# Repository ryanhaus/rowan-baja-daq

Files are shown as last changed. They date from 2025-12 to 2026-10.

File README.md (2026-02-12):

# Rowan University Baja DAQ System
This repository contains all files related to the Data Acqusition (DAQ) system for Rowan University's Baja SAE 2025-2027 team.

All files in this repository are licensed under the [GNU General Public License Version 3.0](LICENSE).

## Components
Click these links to quickly navigate to one of the several components of the DAQ system.
Each link has more detailed information about the design and use of the component.
 - [CAN Module](can-module): Main building block of design, connects other devices together over the CAN bus.

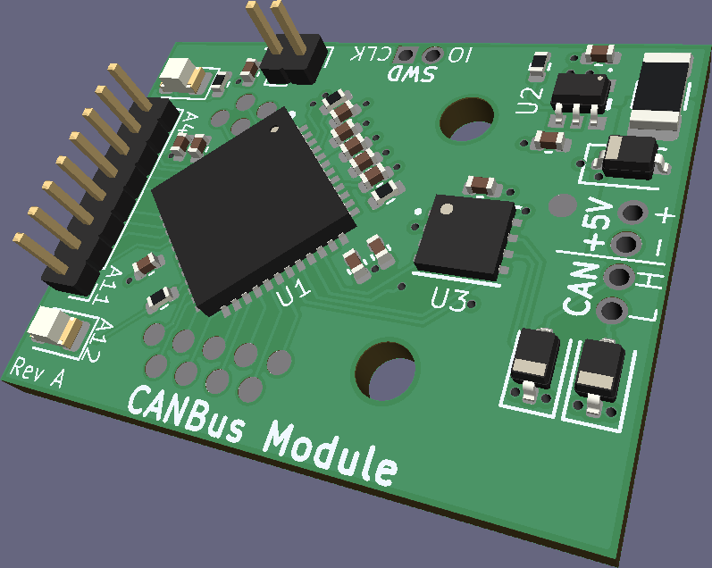
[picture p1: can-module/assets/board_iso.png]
   

 - [Accelerometer Board](accelerometer-board): Contains a 6-axis intertial measurement unit to measure linear and rotational acceleration.

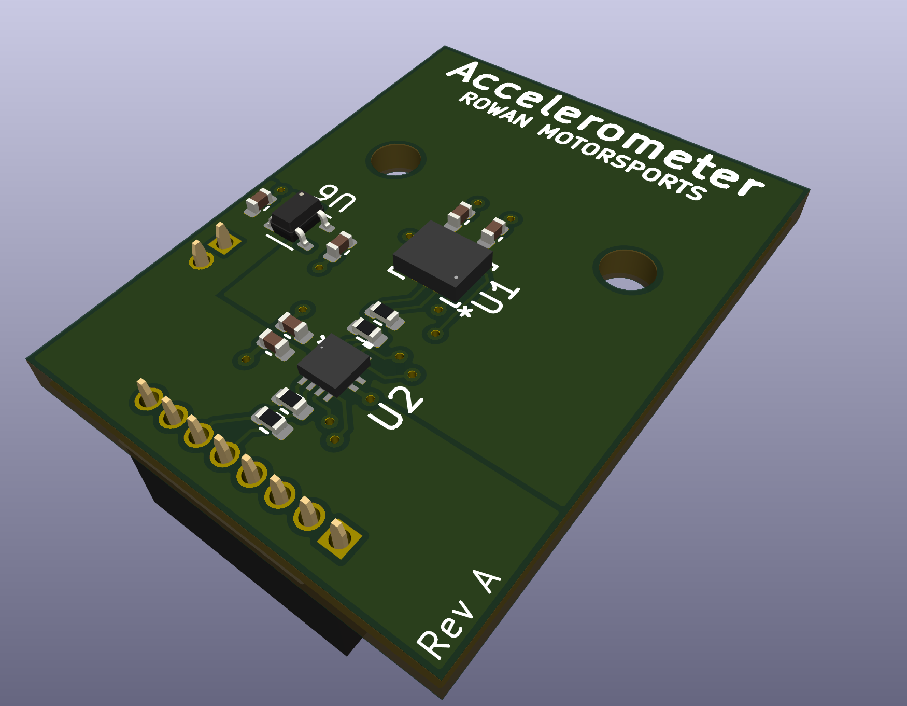
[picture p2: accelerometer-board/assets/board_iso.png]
   

 - [SD Card Board](sd-card-board): Contains a microSD card slot to log data.

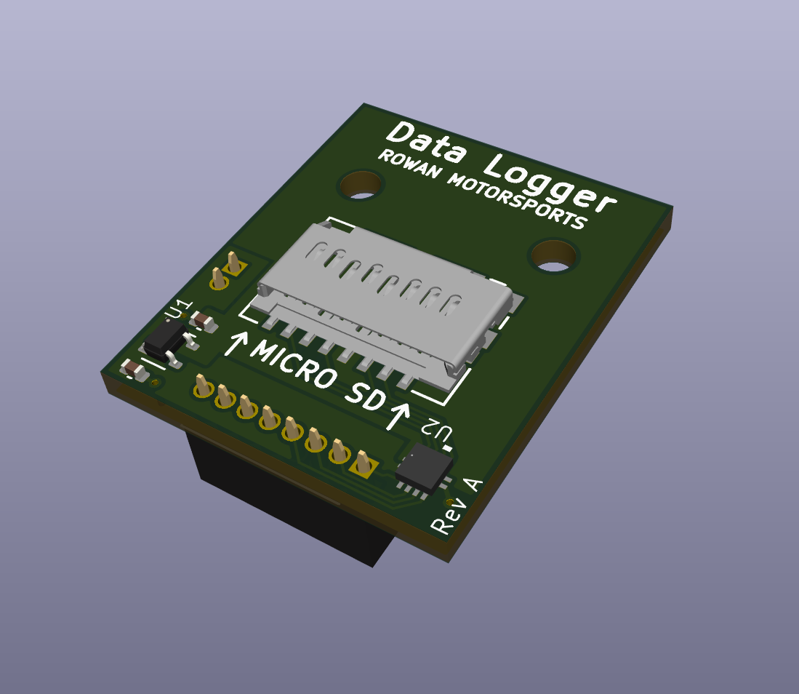
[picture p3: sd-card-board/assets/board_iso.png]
   

 - [Wireless Communication Unit](comm-unit): Contains a LoRa module to wirelessly transmit data.

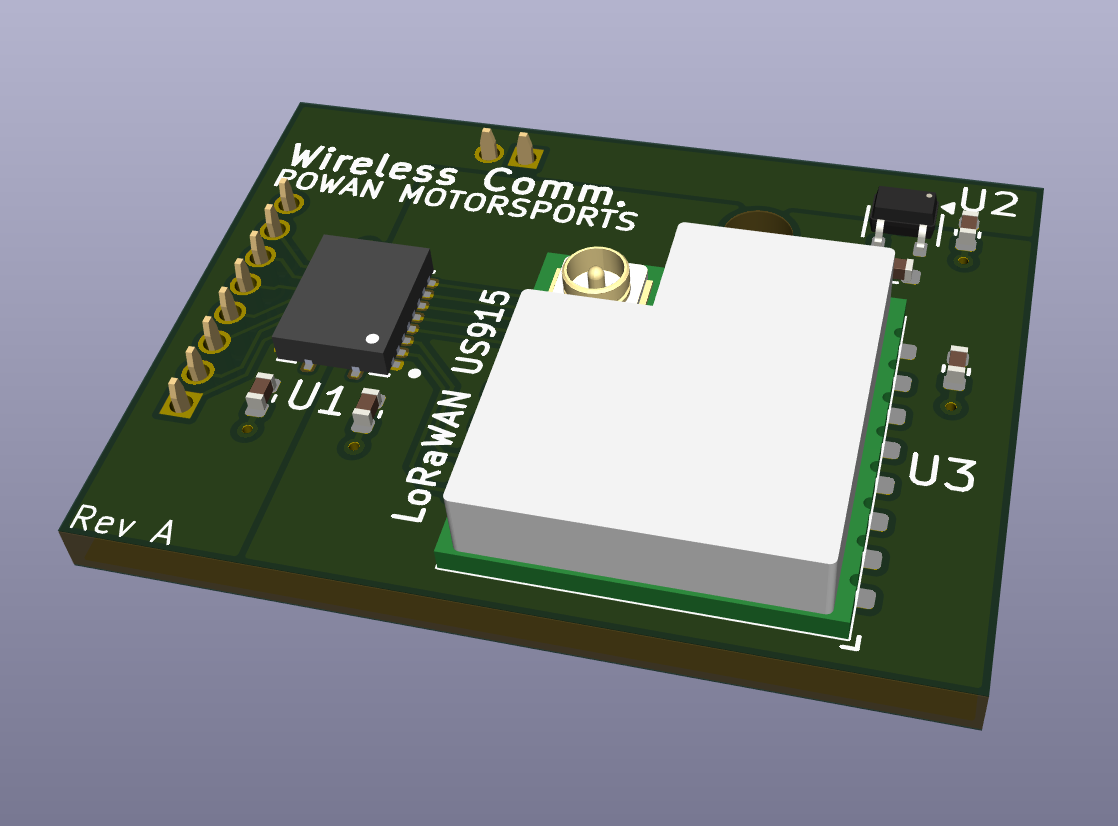
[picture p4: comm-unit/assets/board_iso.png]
   

 - [PMOD Adapter](pmod-adapter): Allows PMOD boards to be attached to the CAN Modules.

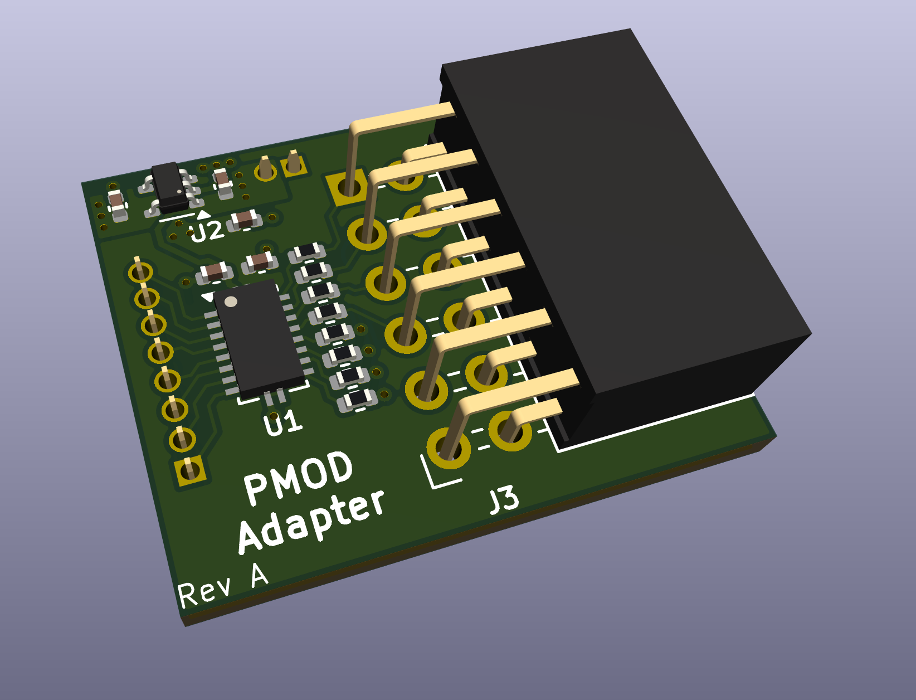
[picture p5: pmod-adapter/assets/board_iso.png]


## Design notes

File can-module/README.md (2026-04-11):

# CAN Module
The CAN Module is the main building block for the overall Data Acquisition system.
It is used as an interface between the shared [CAN Bus](https://en.wikipedia.org/wiki/CAN_bus) and each individual sensor or module around the vehicle.
This document holds all documentation about the components and usage for the CAN Module PCB.

Screenshot of board

See the [software](software) and [pcb](pcb) directories for more info on the respective topics.

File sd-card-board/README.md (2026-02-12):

# SD Card Board
This board is a small data logger board that is designed to mount as a daughterboard for the [CAN Module](../can-module).
A microSD card can be inserted into it and the CAN Module will be able to communicate with the card.
The board features a 5V <=> 3.3V logic level converter to allow communication between the CAN Module and the microSD card.

Board

> [!NOTE]
> The SD card will be operating in SPI mode, so data bandwidth will be somewhat limited.

## Schematic
A screenshot of the schematic is below, a higher-quality pdf is available [here](assets/schematic.pdf).

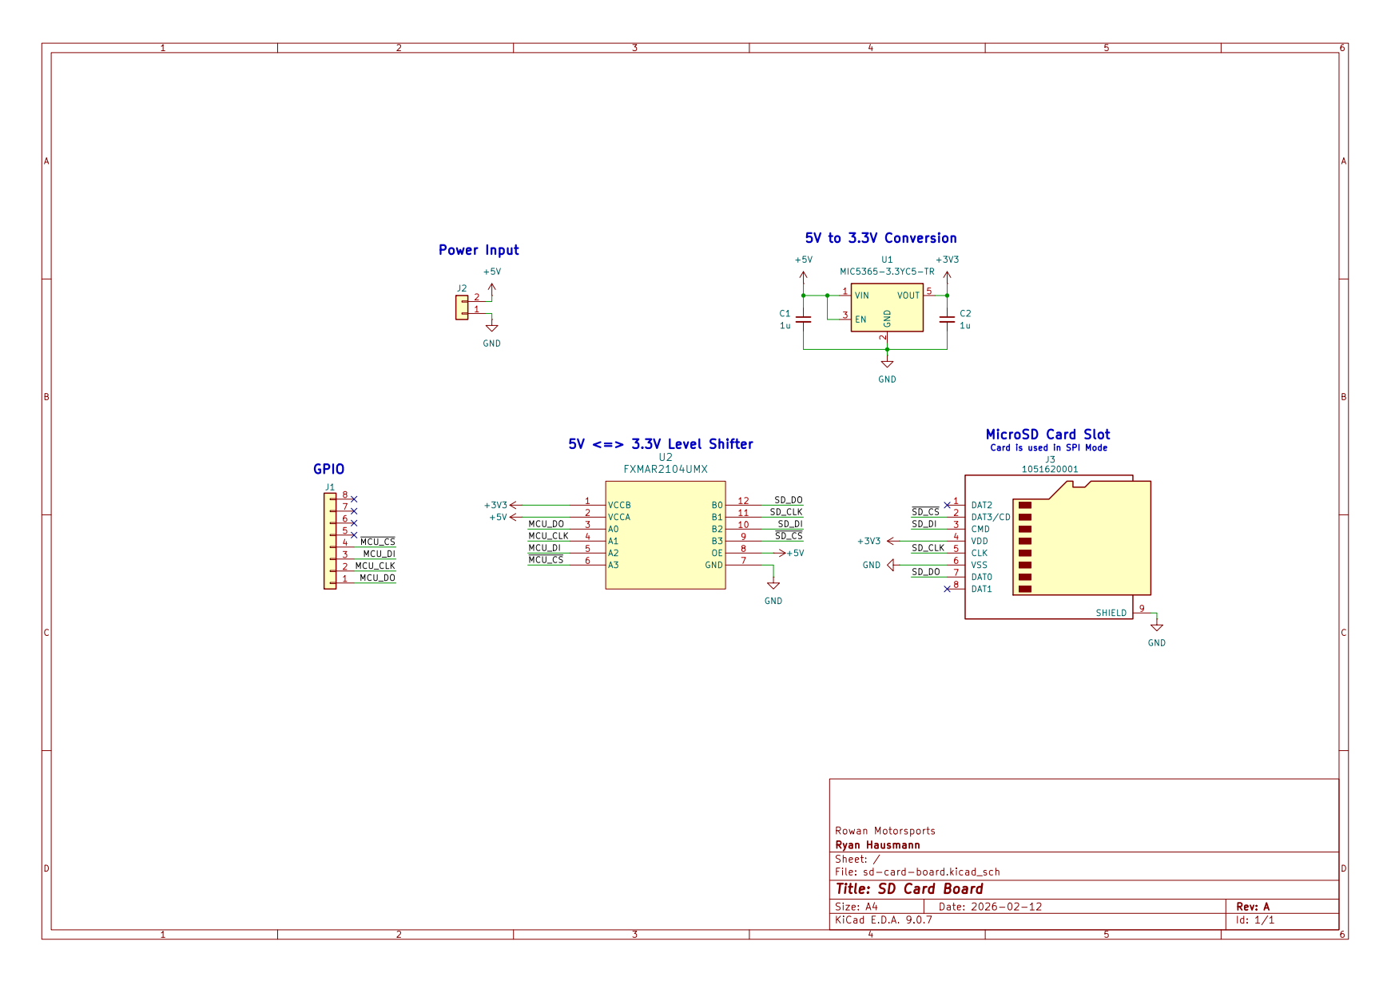
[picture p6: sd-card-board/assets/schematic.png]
Schematic


## Pins
| CAN Module | SD Card Board |
| --- | --- |
| A4 | N/C |
| A5 | N/C |
| A6 | N/C |
| A7 | N/C |
| A8 | CSn |
| A9 | DI |
| A10 | CLK |
| A11 | DO |

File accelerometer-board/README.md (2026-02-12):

# Accelerometer Board
This board features an BMI323 inertial measurement unit w/ a 6-axis accelerometer.
It is meant to be a daughterboard for the [CAN Module](../can-module) and is able to mount to the sensor interface and be attached with 2x M2 mounting screws.
The board also features a 5V <=> 3.3V logic level converter to allow for communication between the CAN Module and the IMU.

Image of board

## Schematic
Screenshot of schematic is below. Higher-quality pdf available [here](assets/schematic.pdf)

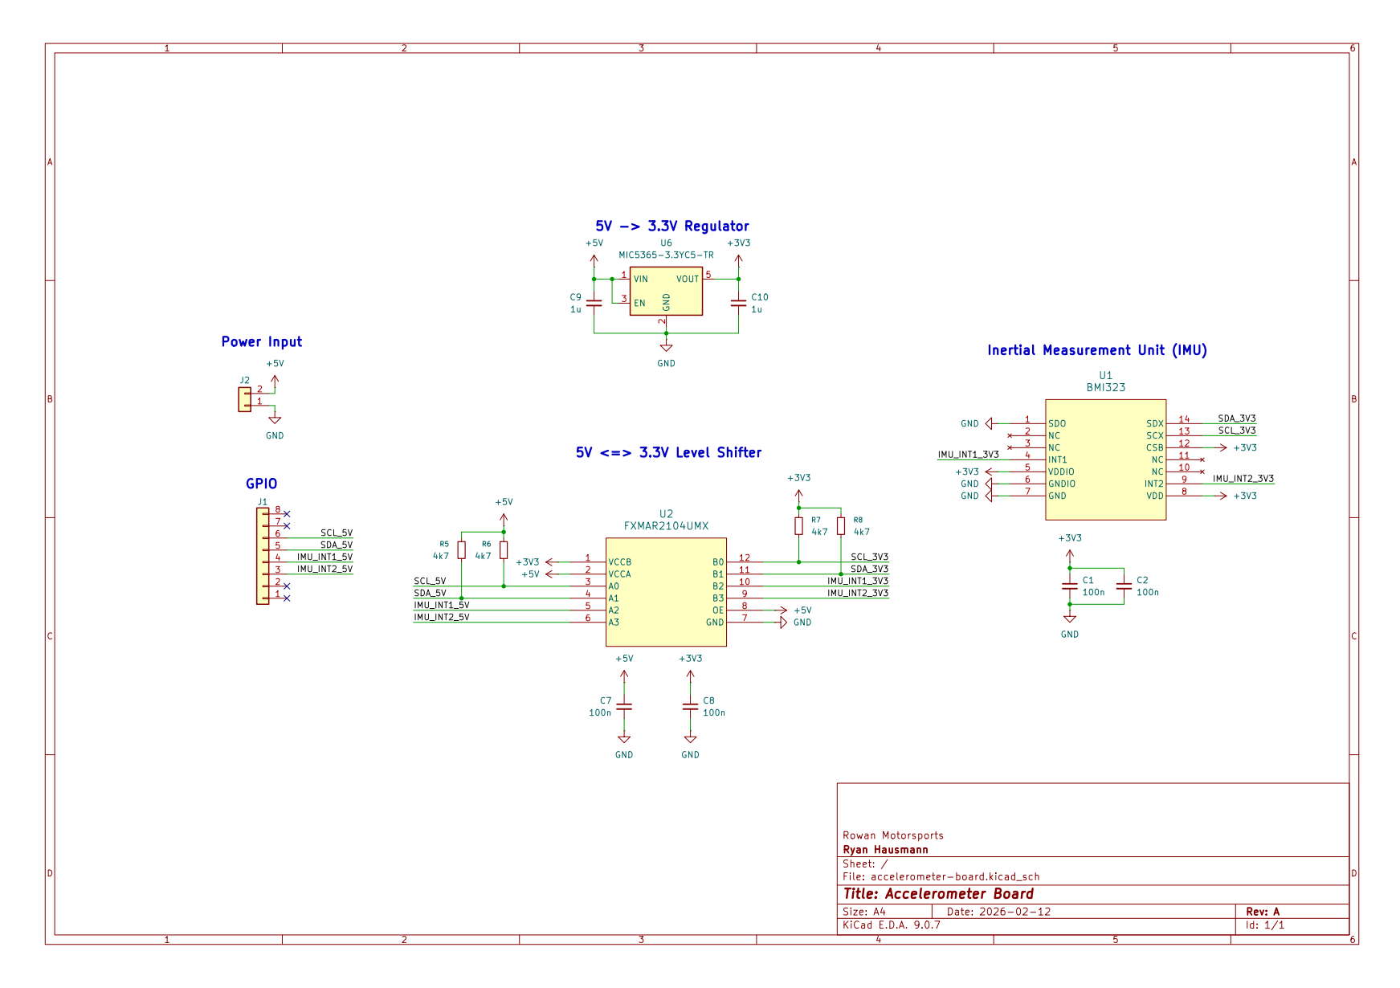
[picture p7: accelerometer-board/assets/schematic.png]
Schematic


## Pins
| CAN Module | Accelerometer Board |
| --- | --- |
| A4 | N/C |
| A5 | N/C |
| A6 | SCL |
| A7 | SDA |
| A8 | Interrupt 1 |
| A9 | Interrupt 2 |
| A10 | N/C |
| A11 | N/C |

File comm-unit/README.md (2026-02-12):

# Wireless Communication Unit
This board features a [Wio-SX1262](https://www.seeedstudio.com/Wio-SX1262-Wireless-Module-p-5981.html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) LoRa module and is used to wirelessly transmit sensor data over long distances (3-5km).
It is designed to be a daughterboard for the [CAN Module](../can-module) and mounts on top of it via the sensor interface.

Board

## Schematic
A screenshot of the schematic is below. A higher-quality pdf is available [here](assets/schematic.pdf).

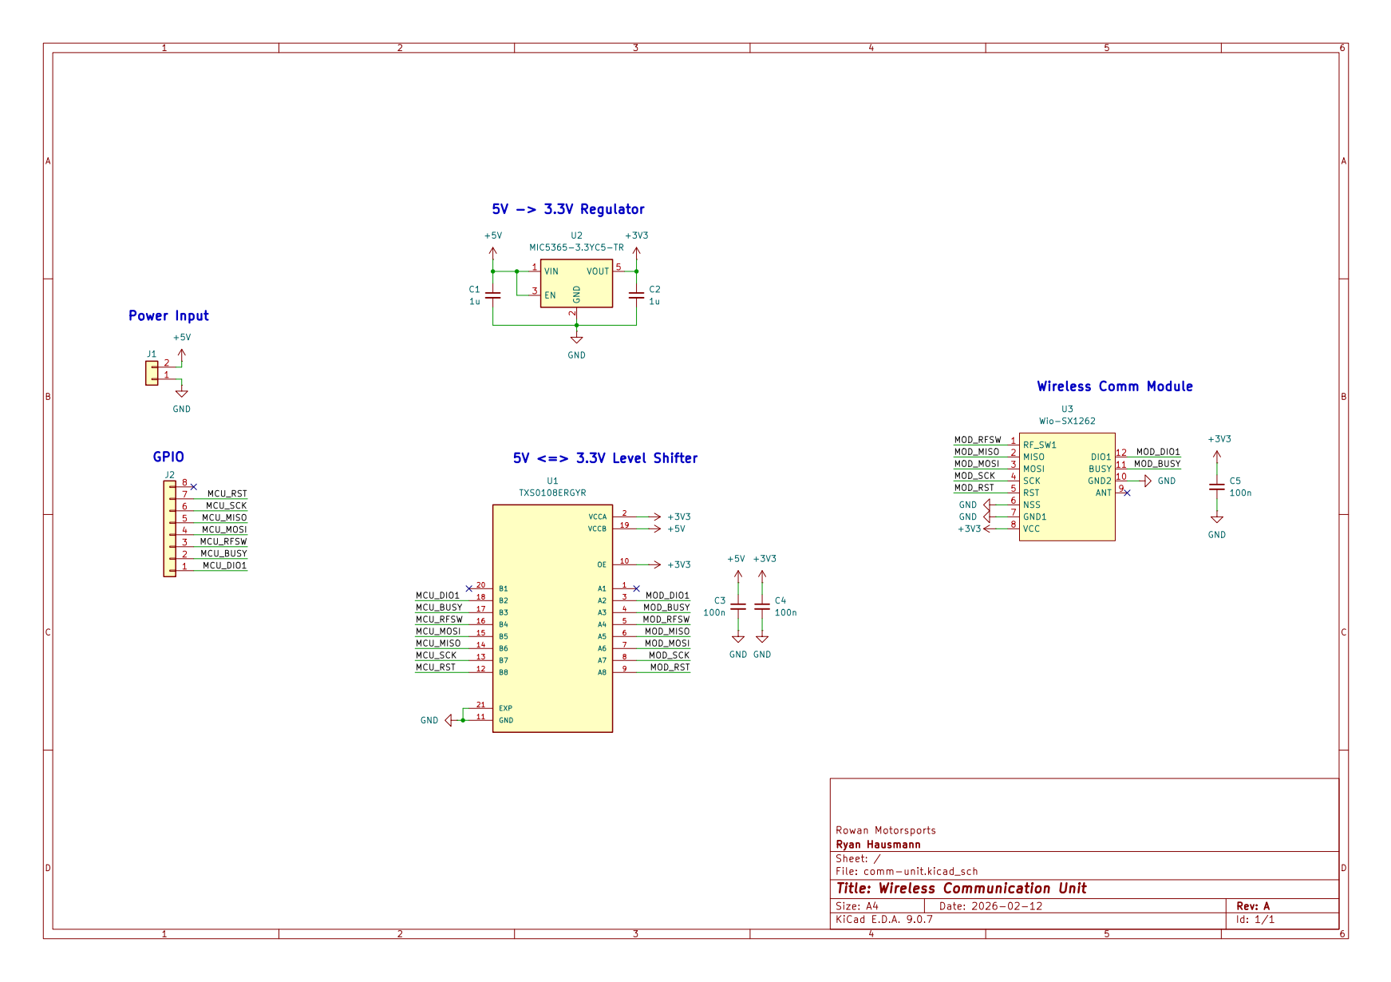
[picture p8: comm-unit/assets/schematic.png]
Schematic


## Pins
| CAN Module | Comm Unit |
| --- | --- |
| A4 | N/C |
| A5 | NRST |
| A6 | SCK |
| A7 | MISO |
| A8 | MOSI |
| A9 | RFSW |
| A10 | BUSY |
| A11 | DIO1 |

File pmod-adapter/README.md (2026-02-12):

# PMOD Adapter
The PMOD adapter is meant to be a daughterboard for the [CAN Module](../can-module).
It is meant to act as an adapter board to convert the 5V logic from the CAN Module into 3.3V logic for the [PMOD interface](https://en.wikipedia.org/wiki/Pmod_Interface) (see the spec [here](https://digilent.com/reference/_media/reference/pmod/pmod-interface-specification-1_2_0.pdf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)), which is commonly used in many [Digilent sensor boards](https://digilent.com/shop/products/fpga-boards/expansion-modules/pmods).
This helps save time when a single sensor needs to be used and it would be impractical to design a custom board just for that, making it easier to simply plug in a PMOD board.

Image of board

## Schematic
Screenshot of schematic is below. Higher quality pdf available [here](assets/schematic.pdf).

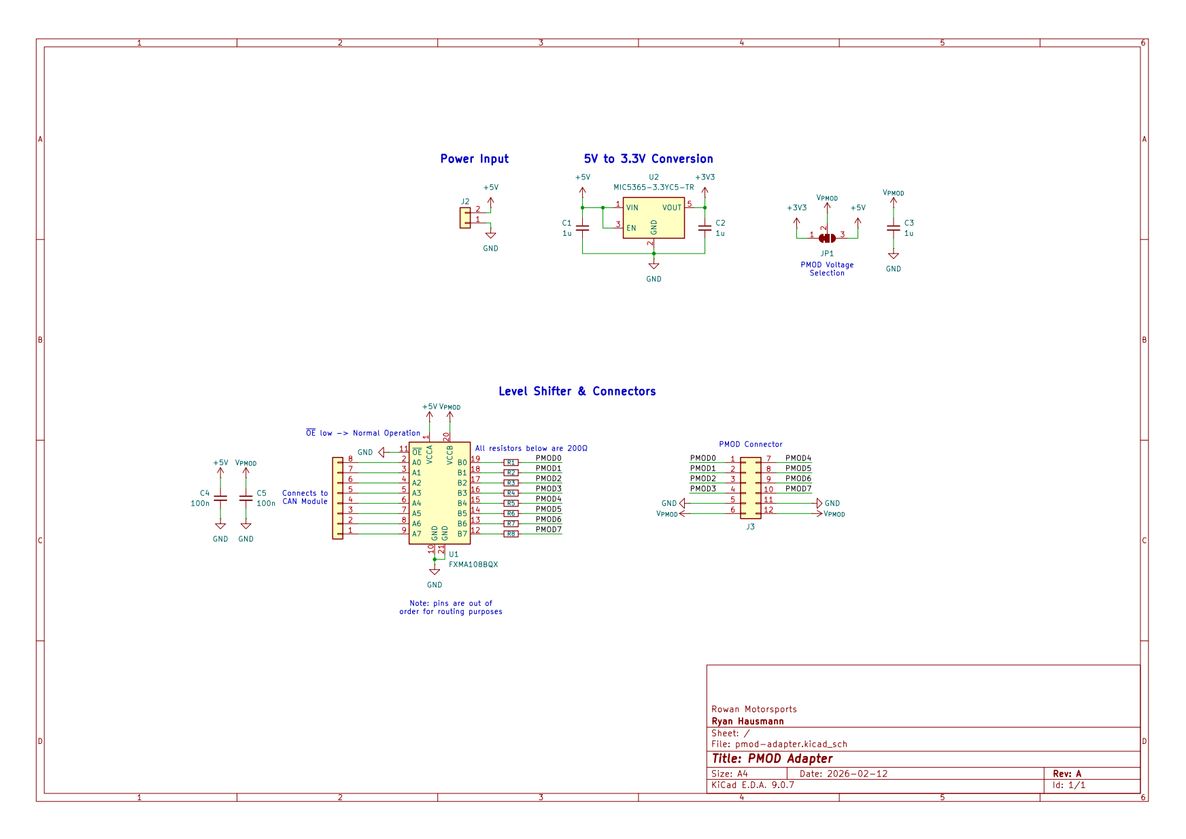
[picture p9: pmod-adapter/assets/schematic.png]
Schematic


## Pins
| CAN Module | PMOD Adapter |
| --- | --- |
| A4 | PMOD 0 |
| A5 | PMOD 1 |
| A6 | PMOD 2 |
| A7 | PMOD 3 |
| A8 | PMOD 4 |
| A9 | PMOD 5 |
| A10 | PMOD 6 |
| A11 | PMOD 7 |

## Extra Information
### Mounting to CAN Module
This board can mount directly onto the sensor interface of the CAN Module via female headers on the bottom of the board.
Note that, due to size constraints, this board does not feature M2 mounting holes.

### Changing the Logic Level
This board supports changing the logic level via a selectable solder bridge on the bottom of the board.
See the top right in the screenshot below:

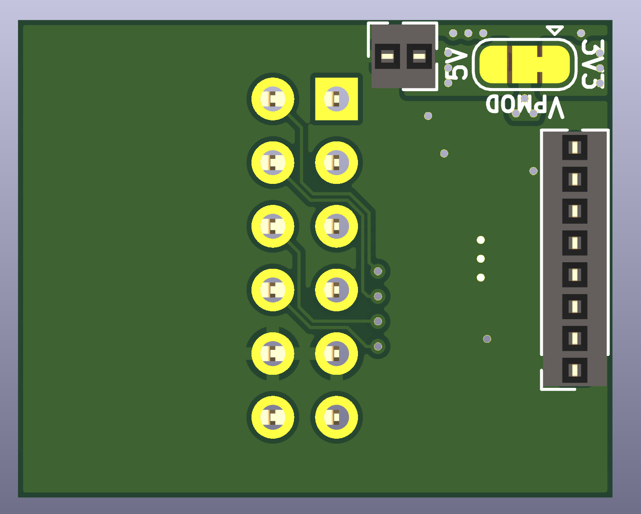
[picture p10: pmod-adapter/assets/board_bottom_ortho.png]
Image of bottom of board


> [!CAUTION]
> Note: When switching the logic level to 5V or something else, note that **the 3.3V bridge will have to be disconnected!!** Otherwise, this bridge will dead-short 5V to 3.3V.

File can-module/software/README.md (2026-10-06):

# Software
The software is written in the C programming language, and uses CMake as the build tool.

> [!NOTE]
> This has only been tested on Linux, unknown if it will work on Windows/Mac.
> If it doesn't work on Windows, you could try using [WSL](https://learn.microsoft.com/en-us/windows/wsl/install).

## Prerequisites
You will need the following:
 - [CMake](https://cmake.org/download/)
 - [MPLAB X IDE](https://www.microchip.com/en-us/tools-resources/develop/mplab-x-ide) (for PIC32 target)
    - You will need to install the packages for '32-bit MCUs' and 'XC32 Compiler' when prompted.
    - When installing the XC32 compiler, check the 'Add to PATH' option when prompted.
 - [ARM GCC Cross Compiler](https://developer.arm.com/downloads/-/gnu-rm) (for RP2040 target)
 - [pkg-config](https://gitlab.freedesktop.org/pkg-config/pkg-config) (for tests only)

### Quickstart on Linux
The following command can be used to install the required packages on Ubuntu or Fedora.
**Note that the XC32 compiler and MPLAB X IDE must be downloaded and installed separately from the vendor, see links above.**

#### Ubuntu
```sh
$ sudo apt install cmake libcriterion-dev pkg-config gcc-arm-none-eabi libnewlib-arm-none-eabi
```

#### Fedora
```sh
$ sudo dnf install cmake pkgconf-pkg-config arm-none-eabi-gcc-cs arm-none-eabi-newlib arm-none-eabi-gcc-cs-c++
$ rpm -ivh https://github.com/samber/criterion-rpm-package/releases/download/2.3.3/libcriterion-devel-2.3.3-2.el7.x86_64.rpm
```
Note that there is no provided package for libcriterion by default on Fedora, so [this](https://github.com/samber/criterion-rpm-package) package is manually installed separately above.
Additionally, libcriterion is only needed for tests.

## Building
To build, run the following:

```sh
$ cmake -B build # Generates CMake files, generally only needed once (unless you edit or add new CMake configs)
$ cmake --build build -j $(nproc) # Actually builds the targets
```

This will create build files and compile the target programs in the `build` directory.

## Running Tests
This project uses the Criterion testing library, which can be ran using CTest (included with CMake).

Tests need to be built within the `tests` directory. To build the tests, run the following within the `tests` directory (same commands for regular building, just run within the `tests` directory):
```sh
$ cmake -B build
$ cmake --build build -j $(nproc)
```

To run tests, run the following:

```sh
$ ctest --test-dir build
```

## Flashing to hardware
### Debugger
I used the [MPLAB SNAP](https://www.microchip.com/en-us/development-tool/pg164100) programmer/debugger connected to the SWD pins on the CAN module.

See Table 3.3.1 in the [user manual](https://ww1.microchip.com/downloads/aemDocuments/documents/DEV/ProductDocuments/UserGuides/MPLAB-Snap-In-Circuit-Debugger-User-Guide-50002787.pdf) to see the pinout needed for SWD. 

Note that the MPLAB SNAP will **not** provide power to the CAN Module, and it needs a voltage reference (5V) connected to the VDD pin. I made a simple wire harness to connect a +5V source to the VDD pin on the MPLAB SNAP and the +5V pin on the CAN Module, as well as connect all grounds. I also added wires to connect the SWDIO and SWCLK pins together between the MPLAB SNAP and CAN Module.

### How to flash PIC32
I used the MPLAB IPE software to flash the generated hex file in the `build/pic32` directory to the microcontroller.

Simply select the device as a `PIC32CM1216JH01048`, select the hex file for the target (located in `build/pic32` as `[name]_pic32.hex`), then click 'Program'.

### How to flash Raspberry Pi Pico (RP2040)
Built file is `build/rp2040/[name]_rp2040.uf2`

Instructions TBD

## Project Structure
This section contains a little bit of information about how the software is structured for this project.

There are several directories here which contain source code files which do different things, being `vendor`, `hal`, `lib`, `targets`, and `tests`.

The `vendor` directory contains files provided by or generated by vendor tools. For example, board template headers generated by MPLAB X IDE are in this folder.

The `hal` directory contains the Hardware Abstraction Layer (HAL) files. These allow for the same program to be run on different platforms, for example, the same program can be run on the CAN Module's microcontroller and also be run in simulation. Each HAL library contains a single header (`.h`) which is included in programs or libraries and a C source file (`.c`) for each implementation. Then, when compiling, CMake automatically links the correct implementation to each platform, ensuring compatability across platforms.

The `lib` directory contains helper libraries that build on the HAL libraries. For example, maybe a library for reading from a specific sensor or writing to an SD card, etc.

The `targets` directory contains each individual target program source code. This has the 'main' function for each program being built. For example, a particular target could use both of the aforementioned libraries to read from a sensor and write the data to an SD card. However, this varies since different targets will need to do different things. Regardless, the automated CMake build process will automatically compile a separate firmware binary for every target.

Finally, the `tests` directory contains software simulation test files for ensuring that everything works.

The below diagram shows what source files get used by other sources. We can see that the HAL uses vendor files and simulation files. Then, we can see that the HAL functions get called in custom libraries or by targets. Note that libraries and targets never call vendor or simulation functions directly, it is always through the HAL to ensure cross-platform compatibility. Finally, we see that test programs may call functions from custom targets or custom libraries.

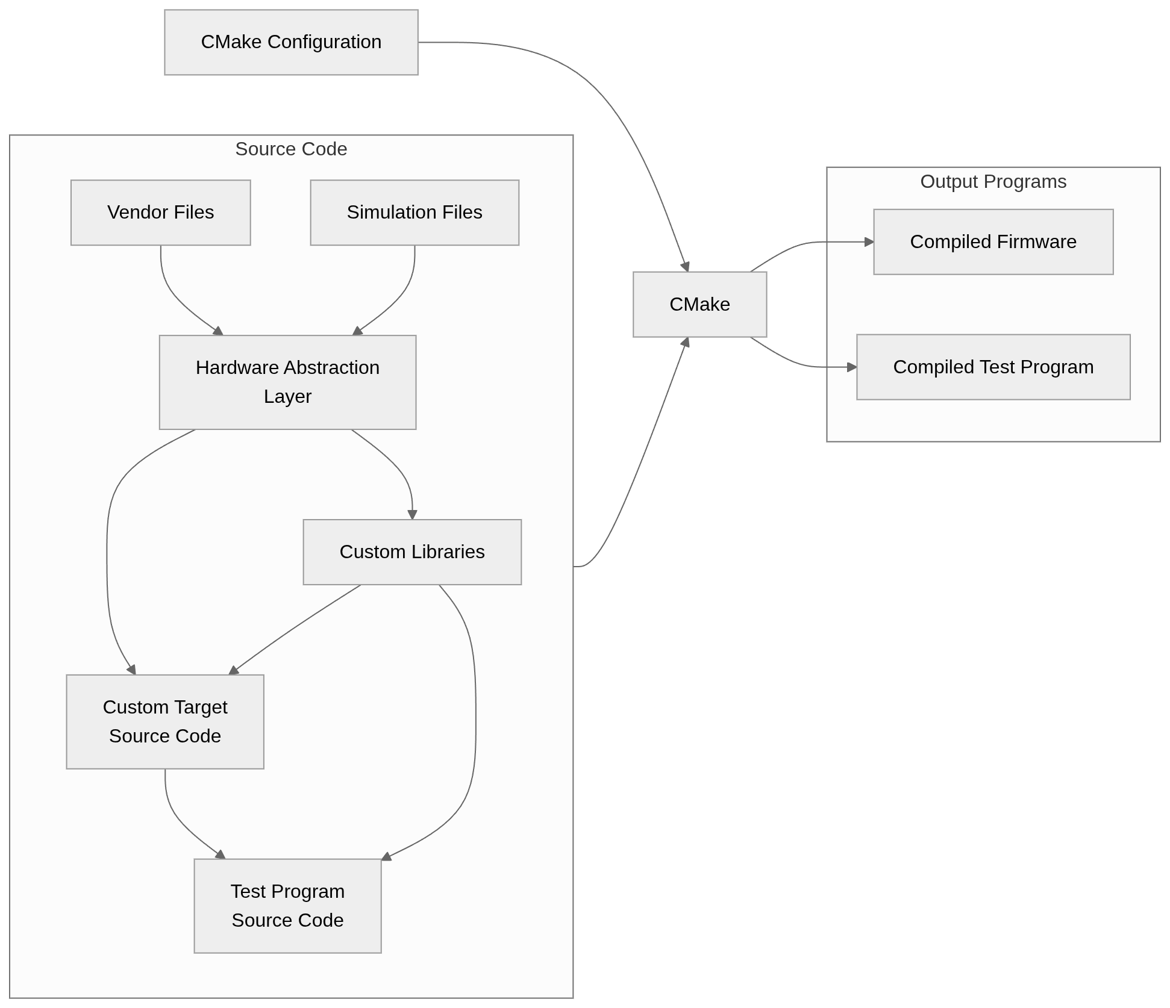
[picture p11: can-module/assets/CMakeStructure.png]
CMAKE Structure


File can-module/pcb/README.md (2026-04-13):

# PCB
The CAN Module is a 1" x 0.75" printed circuit board (PCB) designed in [KiCad](https://kicad.org). All KiCad files are available in the '[pcb](pcb)' directory.

The board features a [48MHz PIC32 microcontroller](#microcontroller), a [CAN Transceiver](#can-transceiver), [headers for power and CAN communication](#vehicle-interface), as well as [8 GPIO pins](#sensor-interface).

Below shows an orthographic top and bottom view of the board:

<div align="center">
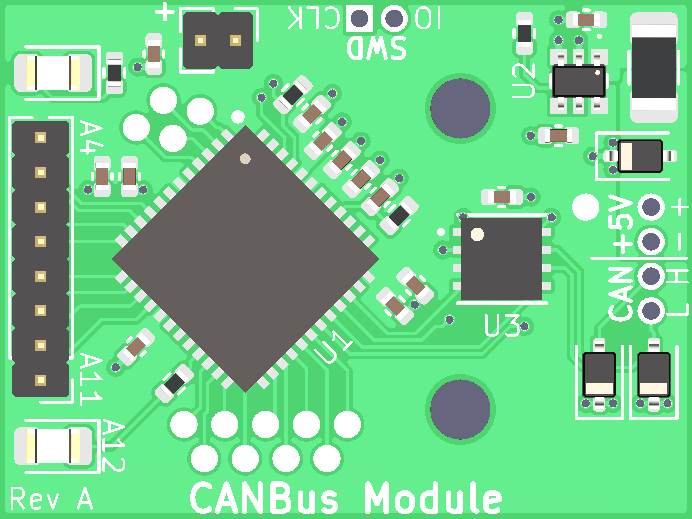
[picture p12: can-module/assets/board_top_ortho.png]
    
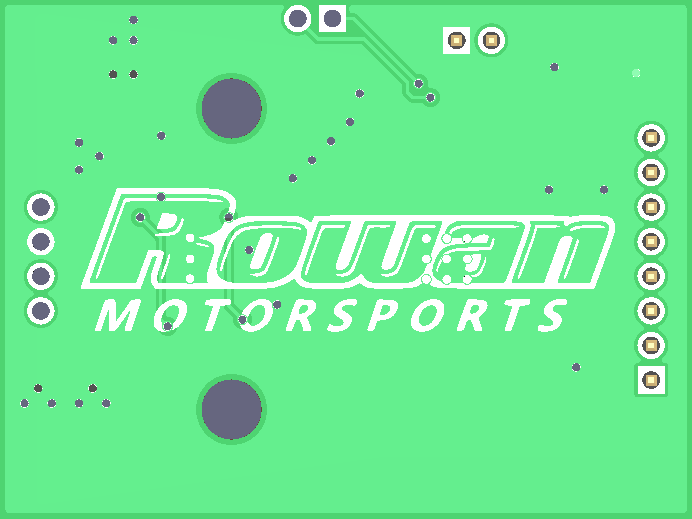
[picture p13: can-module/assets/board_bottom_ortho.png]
    
</div>

> [!NOTE]
> If more than 8 GPIO pins are required for a particular sensor or module, an I2C GPIO expander can be used, or wires can be soldered to one of the exposed GPIO test points (see [here](#extra-gpios)).
> Alternatively, a larger custom board can be designed, these modules are able to communicate with any CAN-FD compatible device that communicates with a 5V logic level.

## Schematic
A schematic of the CAN Module is shown below.
Higher-quality pdf available [here](../assets/schematic.pdf).

Schematic

## Dimensions
The dimensions below may be of use for designing custom enclosures or daughterboards to be mounted to the CAN Module.
All dimensions are in mm, and the mounting holes are M2. Additionally, the pin headers have 0.05" (1.27mm) hole spacing.
Dimensions of board

## Power Requirements
The boards should be powered with +5V DC through the appropriate pins in the [vehicle interface](#vehicle-interface).

The total power consumption depends on attached sensors and modules, but 100-200 mA at most will be consumed by the board itself during peak power usage.

> [!NOTE]
> The boards feature reverse polarity protection, a resettable fuse, and ESD protection diodes on all pins within the vehicle interface.

## Microcontroller
The microcontroller on the CAN Module is the [PIC32CM1216JH01048-I/U5B](https://www.digikey.com/en/products/detail/microchip-technology/PIC32CM1216JH01048-I-U5B/25904014), an inexpensive and tiny 32-bit ARM microcontroller that operates at 48MHz with 128KB of flash and 16KB of RAM, as well as an embedded hardware CAN controller.
See the datasheet [here](https://ww1.microchip.com/downloads/aemDocuments/documents/MCU32/ProductDocuments/DataSheets/PIC32CM-JH00-JH01-Family-Data-Sheet-DS60001632.pdf).



## CAN Transceiver
The CAN Transceiver on the CAN Module is the [ATA6560-GBQW-N](https://www.digikey.com/en/products/detail/microchip-technology/ATA6560-GBQW-N/9453100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).
See the datasheet [here](https://ww1.microchip.com/downloads/en/DeviceDoc/20005991B.pdf).



## Indication LEDs
There are two indication LEDs present on the CAN Module.
One LED is a power indicator LED and is not configurable.
The other is configurable and has the cathode connected through a 30k resistor to the PA12 pin on the microcontroller.
Each LED has 5V at the anode.

## Pins & Connectors
All pins on the CAN Module operate at 5V logic levels by default.
There are two distinct sets of pins on the board that serve different purposes, the sensor interface and the vehicle interface, as described and labelled below.

<div align="center">
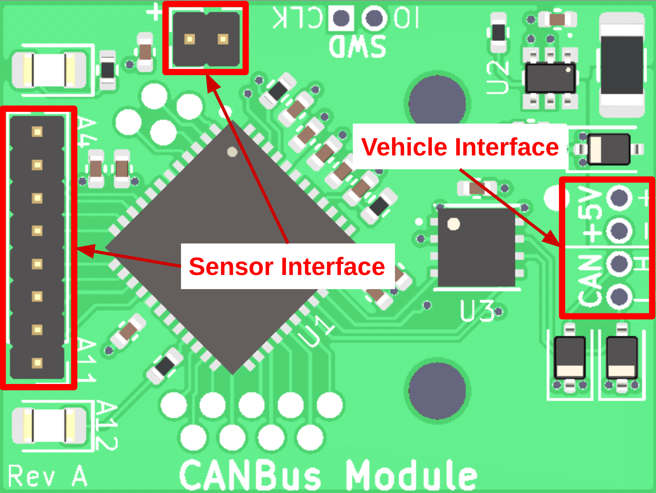
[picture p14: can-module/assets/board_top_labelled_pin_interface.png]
    
</div>

> [!WARNING]
> The headers use **0.05" (1.27mm) hole spacing** for space conservation, not the more common 0.1" (2.54mm) spacing.

### Sensor Interface
The sensor interface is the set of 8 GPIO and 2 output power pins located on the left side of the board.
These pins are intended to provide power to and communicate with some sensor or module, or a custom-designed daughterboard which mounts on top of the CAN Module PCB.

There are two distinct pin headers in the sensor interface, one being 2 pins, and the other being 8 pins.
These are the output power and communication headers, respectively.

The output power header has a positive pin (+5V) and a negative pin (GND), which is labelled appropriately on the board.

The communication header has 8 GPIO pins which are directly connected to GPIO pins on the [microcontroller](#microcontroller).
The pins included in this header include GPIO pins PA4 through PA11 from the microcontroller in sequential order, as labelled on the board.
These pins were selected because every one of them is capable of acting as a communication interface pin for the SERCOM peripheral on the microcontroller, see the [datasheet](https://ww1.microchip.com/downloads/aemDocuments/documents/MCU32/ProductDocuments/DataSheets/PIC32CM-JH00-JH01-Family-Data-Sheet-DS60001632.pdf) (Table 4-2) for more info.

> [!WARNING]
> These pins do not have ESD diodes, series resistors, or short circuit protection (other than what is provided by the microcontroller's GPIO pins).

> [!NOTE]
> Some of these pins are powered by AVDD and some are powered by VDD<sub>IO</sub>.
> While VDD<sub>IO</sub> can be changed to 3.3V to use 3.3V logic, AVDD must remain 5V.
> A future revision of this board could take this into consideration and only expose pins powered by VDD<sub>IO</sub>, so that 3.3V logic can be achieved without external logic level converters.
> Another solution could be to power the entire chip by 3.3V and use an ATA6561 instead of the ATA6560, since the former is able to communicate with 3.3V microcontrollers.

### Vehicle Interface
The vehicle interface is the set of 2 communication and 2 input power pins located on the right side of the board.
These pins are intended to provide power to the CAN Module board and allow for communication between the board and the rest of the vehicle via the shared CAN Bus.

The pins are organized as a single 4-pin header.

### Extra GPIOs
13 extra GPIO pins are exposed from the microcontroller and can be used.
See the screenshot below to see all labelled test points.

<div align="center">
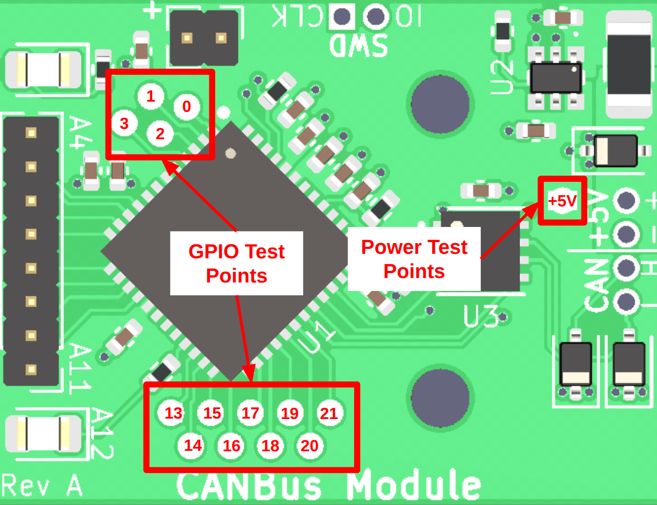
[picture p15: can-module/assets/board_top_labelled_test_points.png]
    
</div>

> [!NOTE]
> All GPIO test points are exposed from Port A, so it is not explicitly labelled in the screenshot.
> For example, the point labelled '13' maps to PA13, '14' to PA14, etc.

> [!NOTE]
> In addition to GPIOs, there is also a test point for +5V.
> This test point is after all power filtering & fusing, so it may be helpful for debugging power issues.

### Programming/Debug Pins
Two serial-wire debug (SWD) pins are exposed and labelled on the back of the board.
A SWD-capable interface will be required to program the boards.

> [!NOTE]
> This is TBD, the boards have not been manufactured yet.

## Connecting to Other Modules
In order to interface with other devices (i.e., other CAN Modules), they must be wired on the same shared CAN Bus.
An example layout is shown below:

CAN Layout Example

Note that every module shares the same four wires that are routed throughout the vehicle.
This topology helps significantly reduce the amount of wire required, time spent routing wire, and helps decentralize devices to minimize single points of failure.

Also note that CAN Bus Modules generally do not exist on their own, they will probably need some other attached device or sensor to either provide or process data on the bus.

See [here](https://en.wikipedia.org/wiki/CAN_bus) for more info on CAN Bus.

> [!WARNING]
> Make sure that the CAN bus is properly terminated, see [here](https://support.maxongroup.com/hc/en-us/articles/360009241840-CAN-bus-topology-and-bus-termination) for more info.

## Updating This Project
After changes are made to the project, [KiBot](https://github.com/INTI-CMNB/KiBot) (must be installed) can be used to automatically create renders of the schematic and PCB used in this documentation.

Navigate to the `pcb` directory, and run the following:
```sh
$ kibot
```

This command will automatically run the DRC and generate renders.
See [`can-module.kibot.yaml`](pcb/can-module.kibot.yaml) for the configuration.

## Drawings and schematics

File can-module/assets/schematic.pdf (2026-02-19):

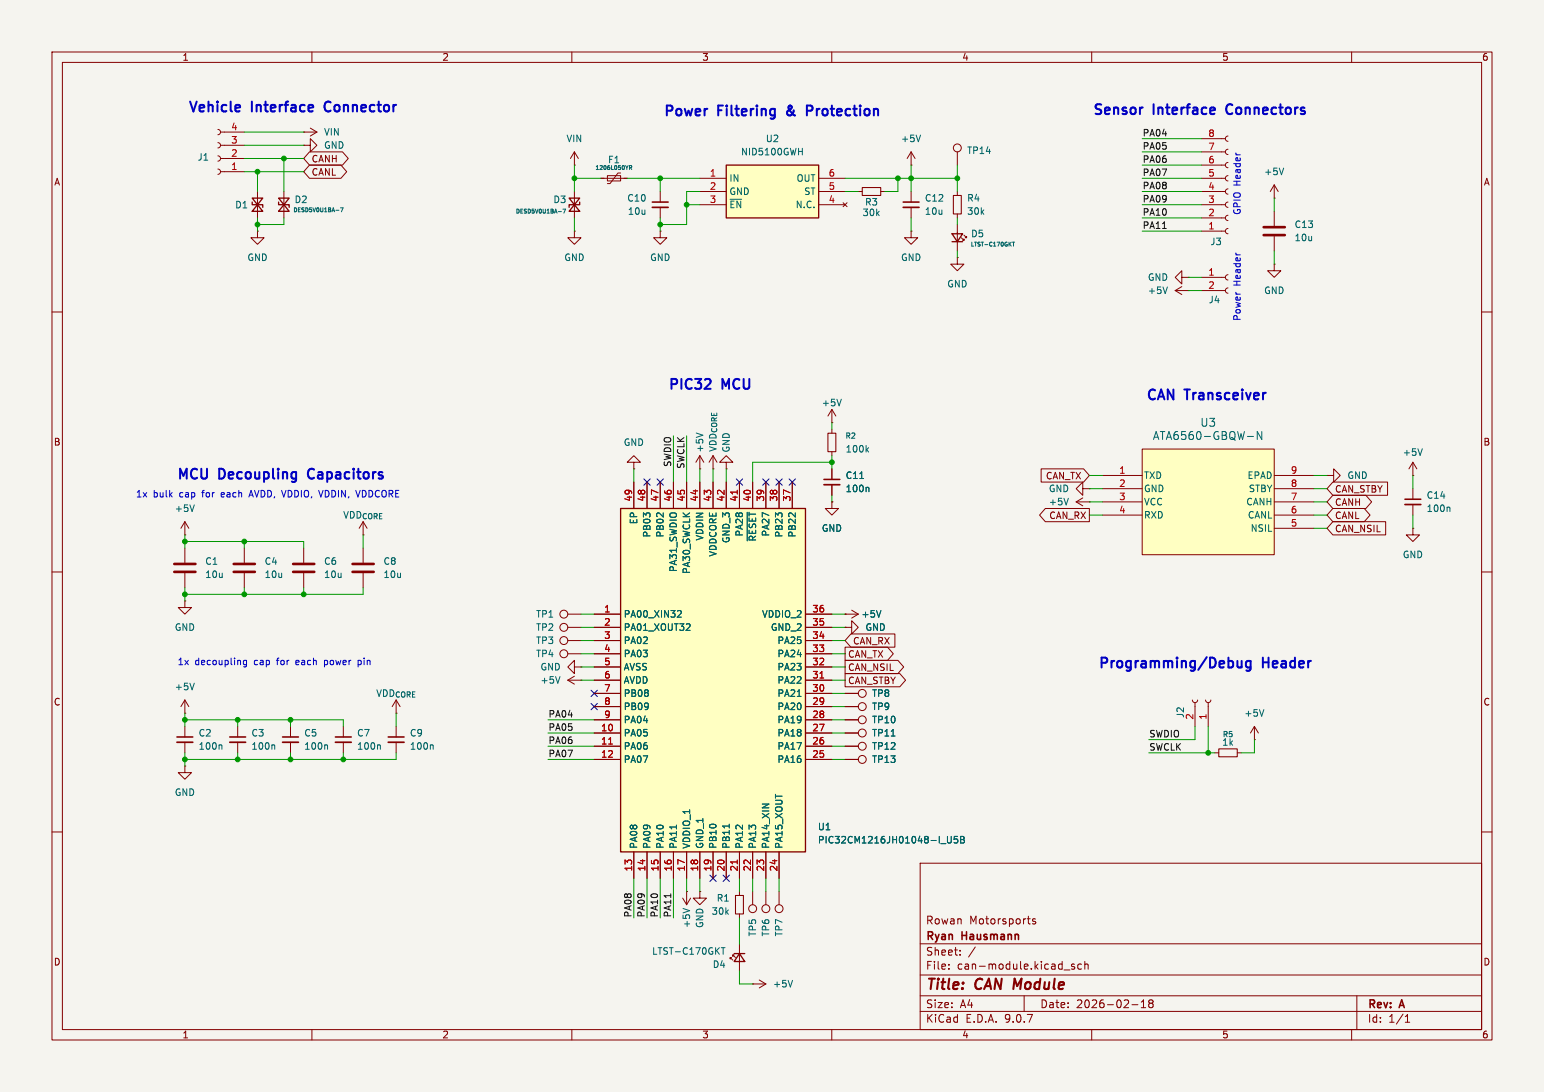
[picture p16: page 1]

1x bulk cap for each AVDD, VDDIO, VDDIN, VDDCORE

Id: 1/1 Title: CAN Module

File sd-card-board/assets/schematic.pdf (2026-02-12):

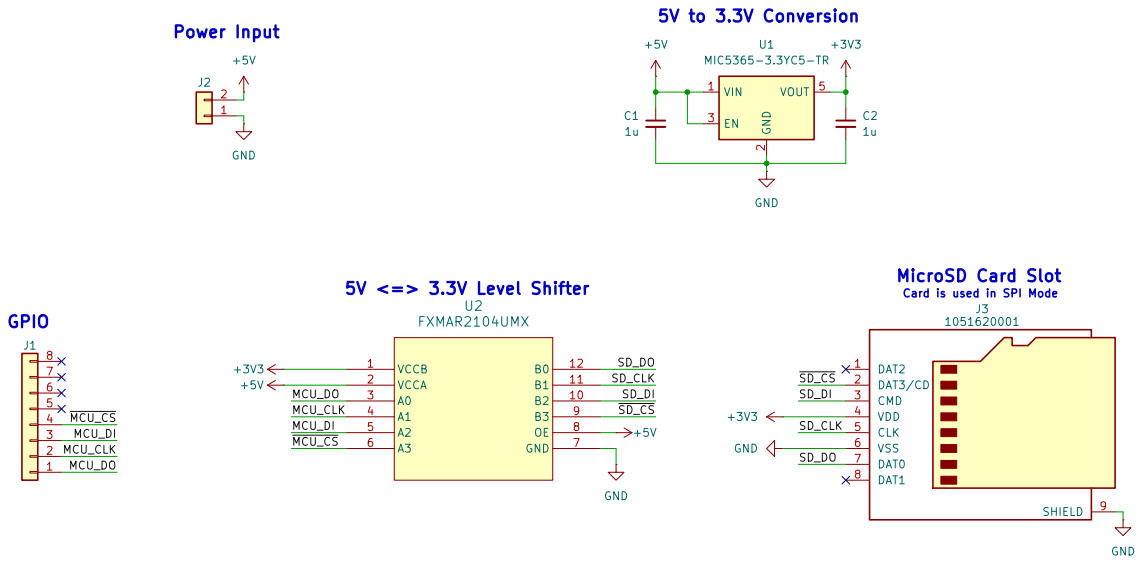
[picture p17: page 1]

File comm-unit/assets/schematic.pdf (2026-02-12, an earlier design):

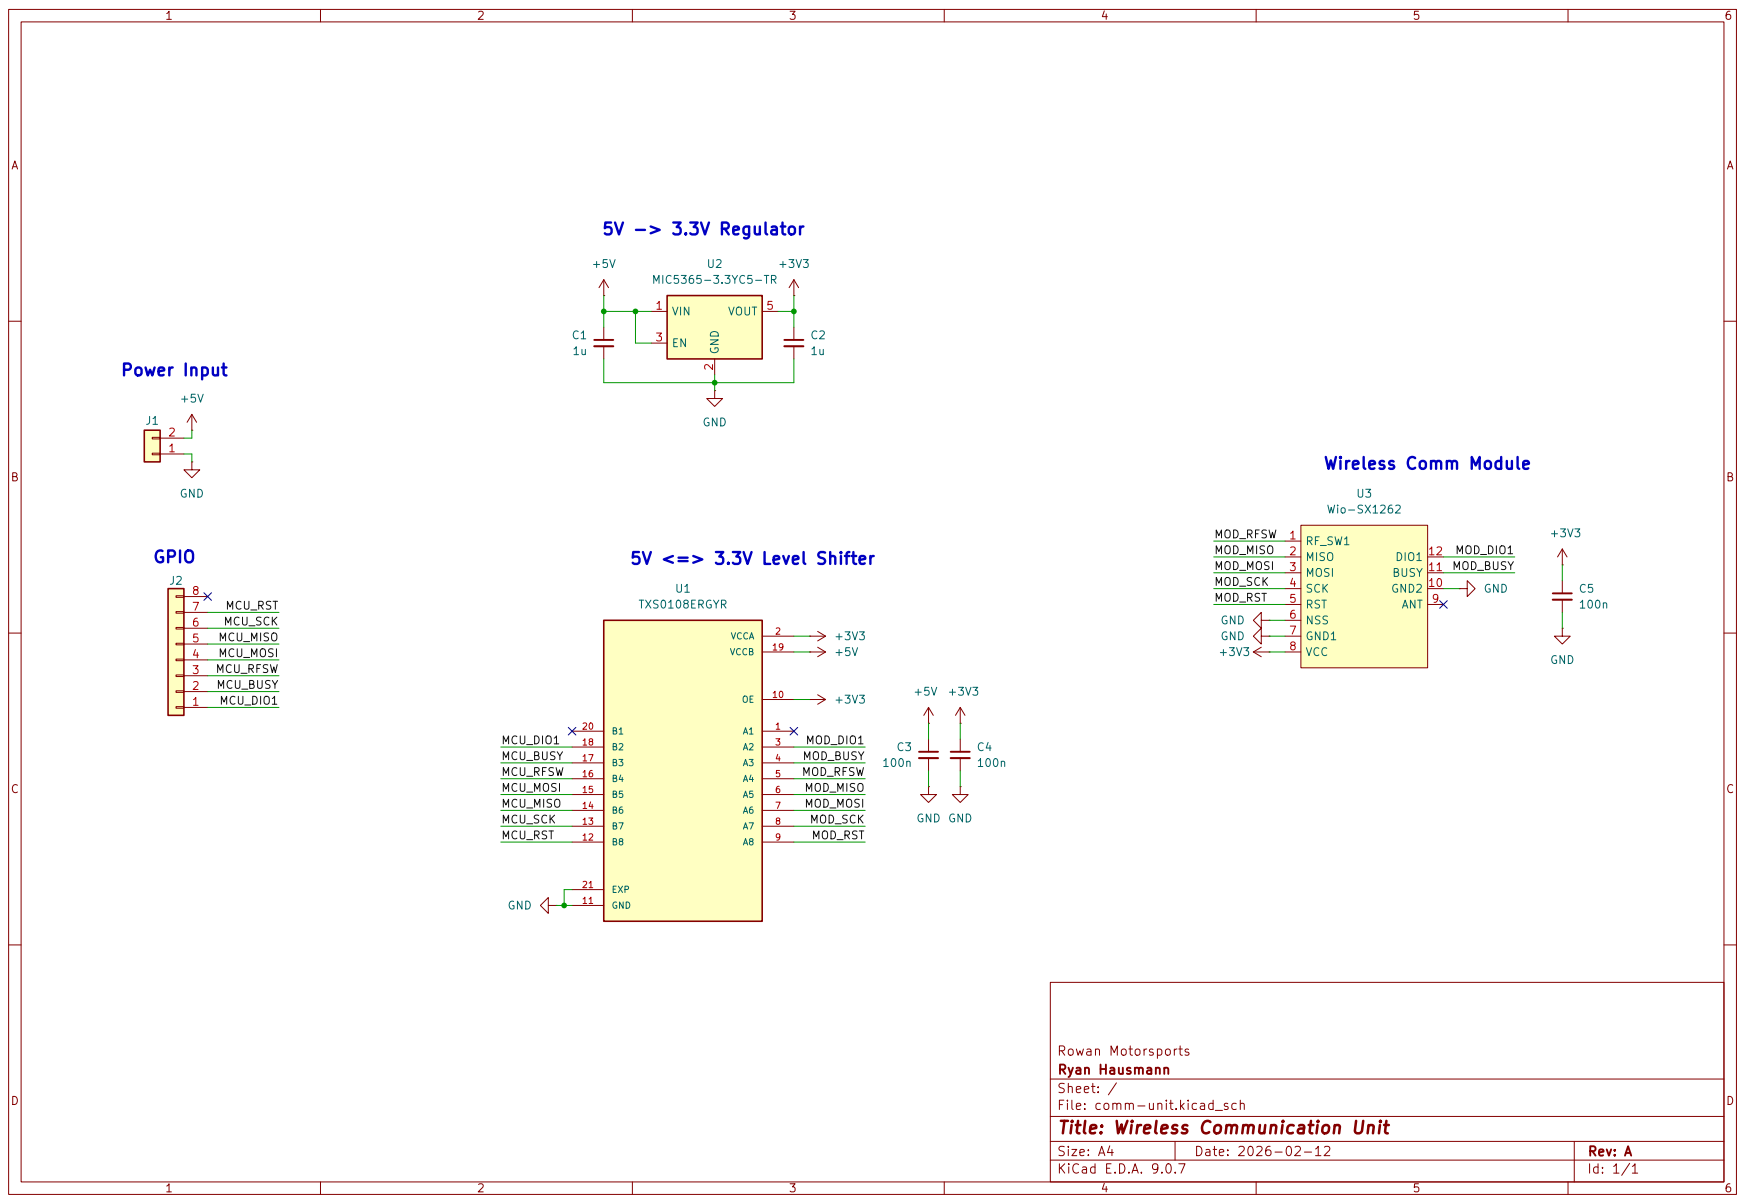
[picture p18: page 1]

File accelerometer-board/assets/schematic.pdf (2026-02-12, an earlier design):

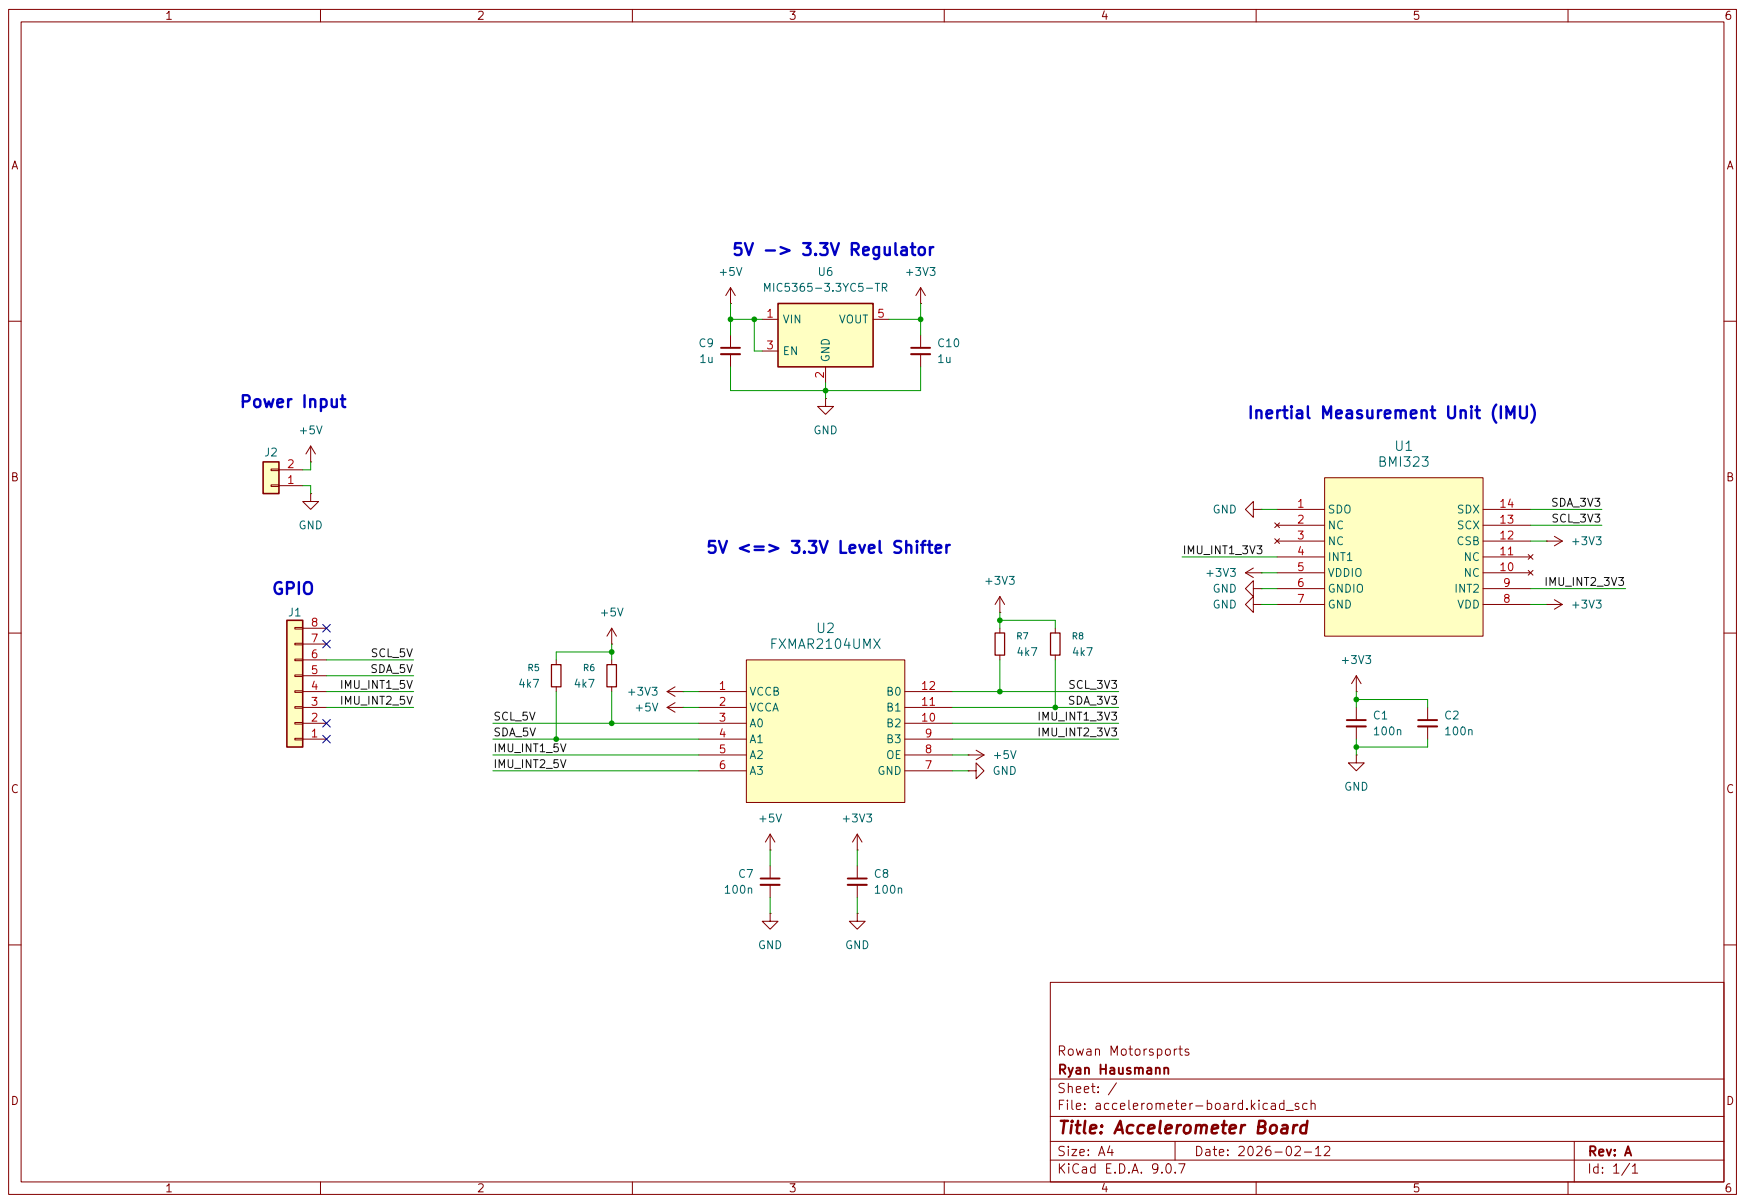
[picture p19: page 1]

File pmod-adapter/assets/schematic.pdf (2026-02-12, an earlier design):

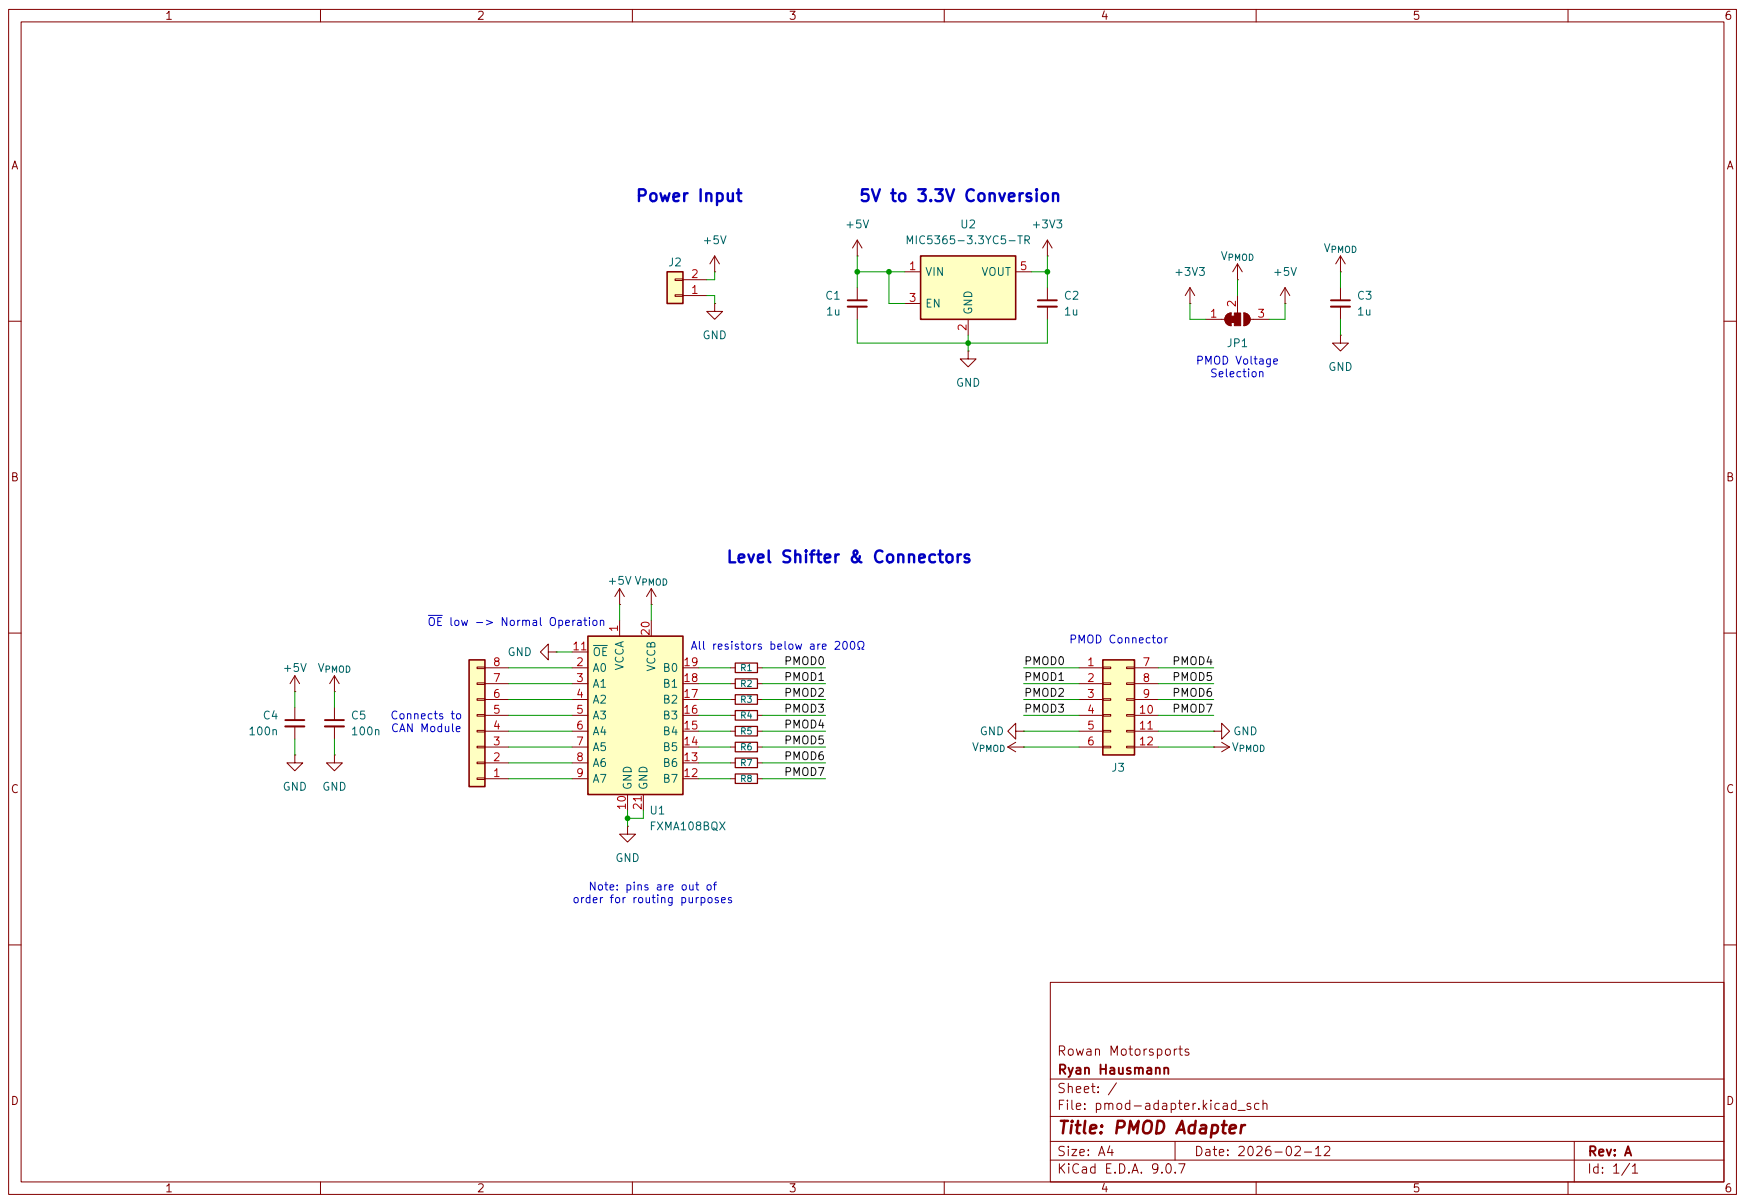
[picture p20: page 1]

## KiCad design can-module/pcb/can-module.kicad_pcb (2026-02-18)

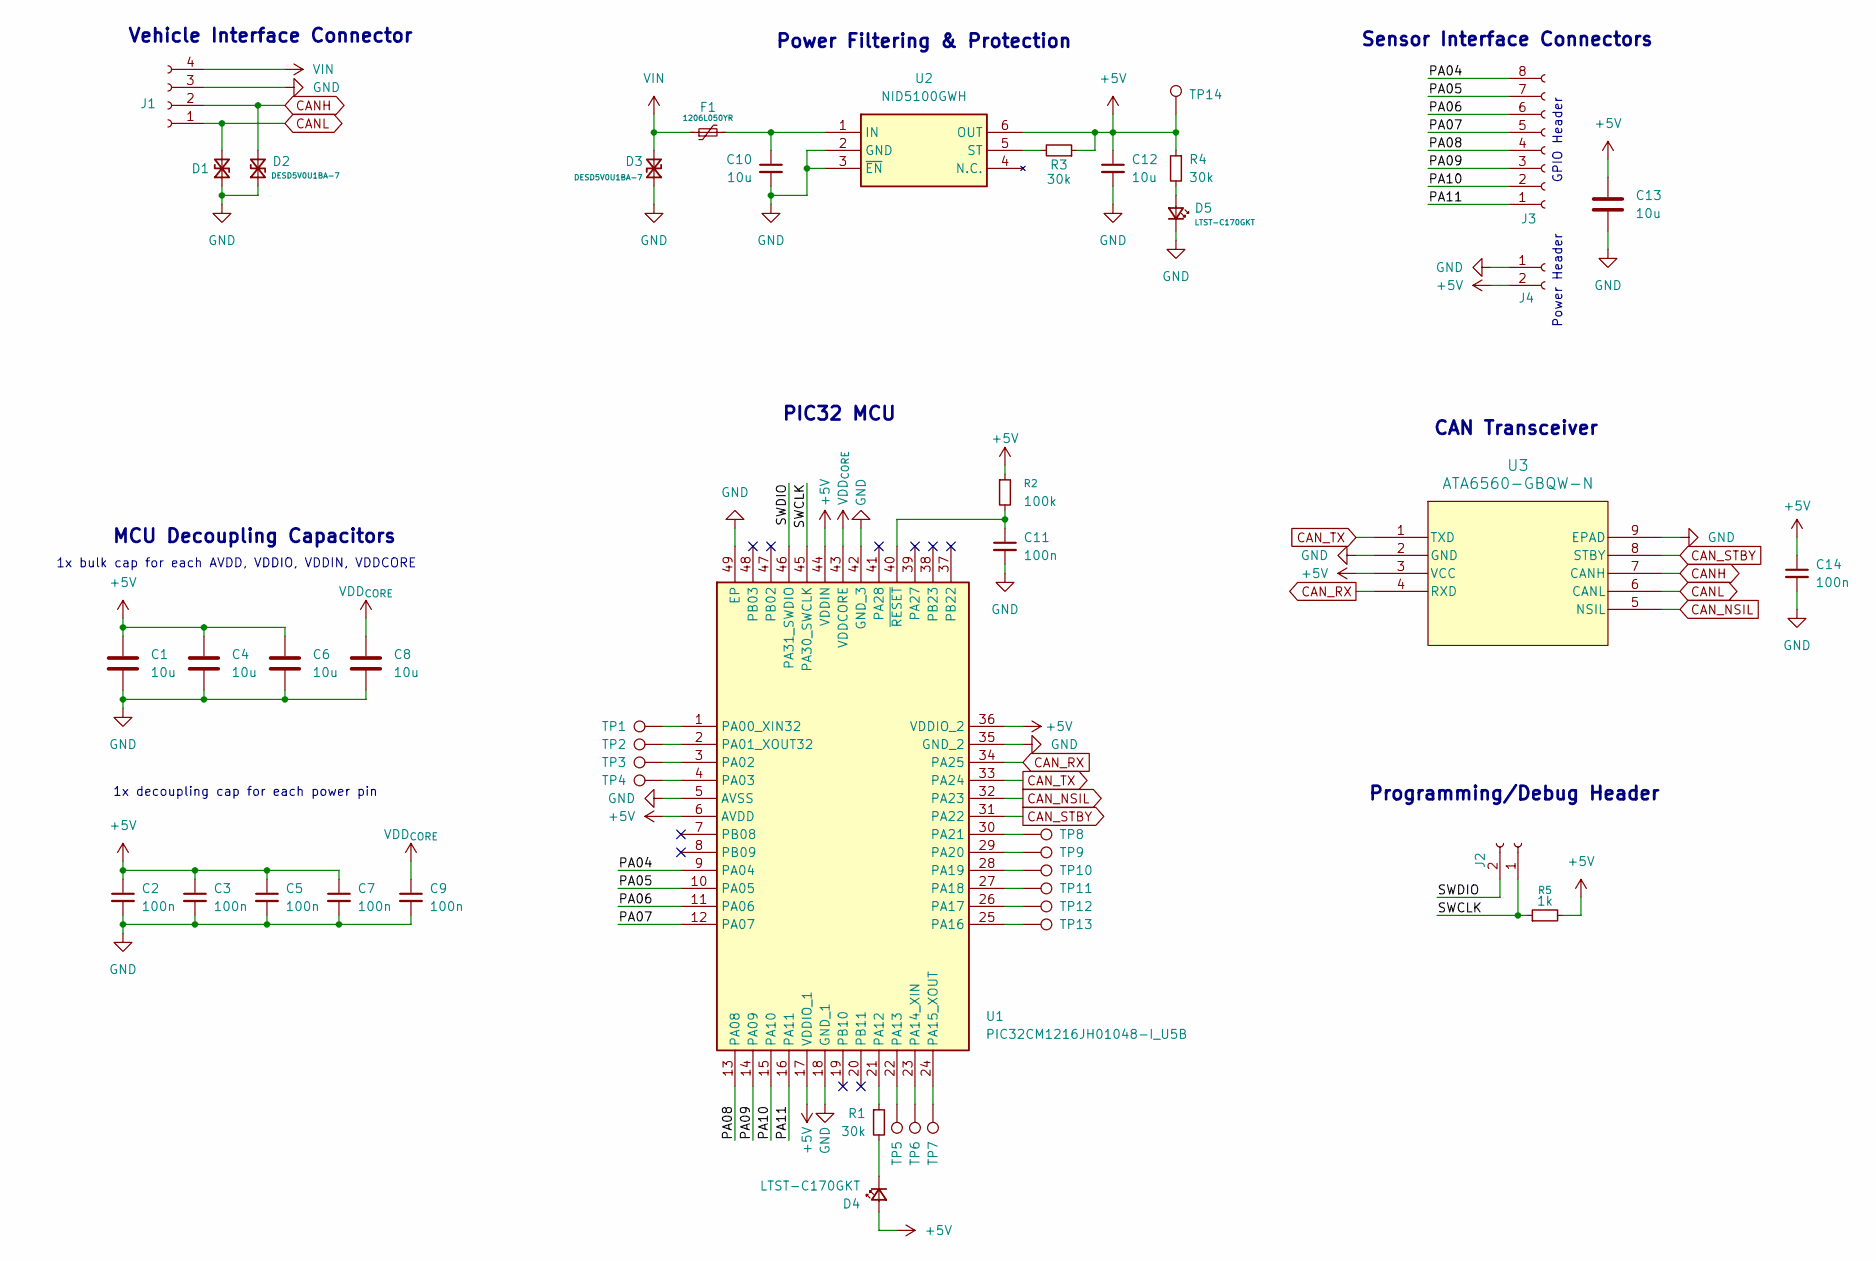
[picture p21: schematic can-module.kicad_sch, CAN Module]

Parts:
C1, C4, C6, C8, C10, C12, C13: 10u; C_0402_1005Metric
C2, C3, C5, C7, C9, C11, C14: 100n; C_0402_1005Metric
D1, D2, D3: DESD5V0U1BA-7; D_SOD-323
D4, D5: LTST-C170GKT; LED_0805_2012Metric
F1: 1206L050YR; Fuse_1206_3216Metric
J1: Conn_01x04_Socket; PinHeader_1x04_P1.27mm_Vertical
J2, J4: Conn_01x02_Socket; PinHeader_1x02_P1.27mm_Vertical
J3: Conn_01x08_Socket; PinHeader_1x08_P1.27mm_Vertical
R1, R3, R4: 30k; R_0402_1005Metric
R2: 100k; R_0402_1005Metric
R5: 1k; R_0402_1005Metric
TP1, TP2, TP3, TP4, TP5, TP6, TP7, TP8, TP9, TP10, TP11, TP12, TP13, TP14: TestPoint; TestPoint_Pad_D1.0mm_TightSpacing
U1: PIC32CM1216JH01048-I_U5B; QFN50P700X700X90-49N-D; Manufacturer_Part_Number PIC32CM1216JH01048-I/U5B
U2: NID5100GWH; Manufacturer_Part_Number NID5100GWH; Mouser Part Number 771-NID5100GWH
U3: ATA6560-GBQW-N; VDFN8_3X3_MCH

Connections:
+5V: C1.1, C2.1, C3.1, C4.1, C5.1, C6.1, C7.1, C12.1, C13.1, C14.1, D4.2 (A), J4.2, R2.1, R3.1, R4.1, R5.2, TP14.1, U1.6 (AVDD), U1.17 (VDDIO_1), U1.36 (VDDIO_2), U1.44 (VDDIN), U2.6 (OUT), U3.3 (VCC)
/PA04: J3.8, U1.9 (PA04)
/PA05: J3.7, U1.10 (PA05)
/PA06: J3.6, U1.11 (PA06)
/PA07: J3.5, U1.12 (PA07)
/PA08: J3.4, U1.13 (PA08)
/PA09: J3.3, U1.14 (PA09)
/PA10: J3.2, U1.15 (PA10)
/PA11: J3.1, U1.16 (PA11)
/SWCLK: J2.1, R5.1, U1.45 (PA30_SWCLK)
/SWDIO: J2.2, U1.46 (PA31_SWDIO)
CANH: D2.2 (A2), J1.2, U3.7 (CANH)
CANL: D1.2 (A2), J1.1, U3.6 (CANL)
CAN_NSIL: U1.32 (PA23), U3.5 (NSIL)
CAN_RX: U1.34 (PA25), U3.4 (RXD)
CAN_STBY: U1.31 (PA22), U3.8 (STBY)
CAN_TX: U1.33 (PA24), U3.1 (TXD)
GND: C1.2, C2.2, C3.2, C4.2, C5.2, C6.2, C7.2, C8.2, C9.2, C10.2, C11.2, C12.2, C13.2, C14.2, D1.1 (A1), D2.1 (A1), D3.1 (A1), D5.1 (K), J1.3, J4.1, U1.5 (AVSS), U1.18 (GND_1), U1.35 (GND_2), U1.42 (GND_3), U1.49 (EP), U2.2 (GND), U2.3 (~EN), U3.2 (GND), U3.9 (EPAD)
unnamed: D4.1 (K), R1.2
unnamed: D5.2 (A), R4.2
unnamed: TP1.1, U1.1 (PA00_XIN32)
unnamed: TP2.1, U1.2 (PA01_XOUT32)
unnamed: TP3.1, U1.3 (PA02)
unnamed: TP4.1, U1.4 (PA03)
unnamed: R1.1, U1.21 (PA12)
unnamed: TP5.1, U1.22 (PA13)
unnamed: TP6.1, U1.23 (PA14_XIN)
unnamed: TP7.1, U1.24 (PA15_XOUT)
unnamed: TP13.1, U1.25 (PA16)
unnamed: TP12.1, U1.26 (PA17)
unnamed: TP11.1, U1.27 (PA18)
unnamed: TP10.1, U1.28 (PA19)
unnamed: TP9.1, U1.29 (PA20)
unnamed: TP8.1, U1.30 (PA21)
unnamed: C11.1, R2.2, U1.40 (~RESET)
unnamed: C10.1, F1.2, U2.1 (IN)
unnamed: R3.2, U2.5 (ST)
VDD_{CORE}: C8.1, C9.1, U1.43 (VDDCORE)
VIN: D3.2 (A2), F1.1, J1.4

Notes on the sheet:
1x decoupling cap for each power pin
Sensor Interface Connectors
Vehicle Interface Connector
MCU Decoupling Capacitors
Power Header
Power Filtering & Protection
CAN Transceiver
1x bulk cap for each AVDD, VDDIO, VDDIN, VDDCORE
PIC32 MCU
Programming/Debug Header
GPIO Header

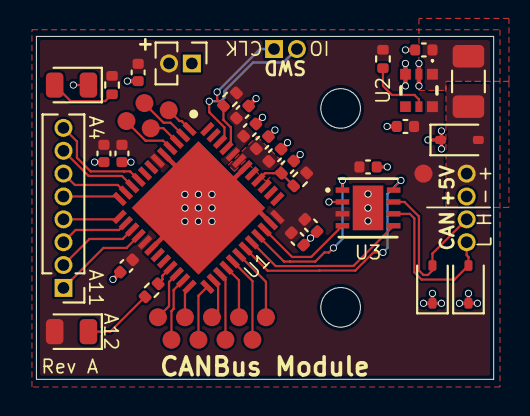
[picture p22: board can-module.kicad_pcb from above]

Board: 2 copper layers, 25.4 x 19.0 mm, 46 parts (0 on the bottom side), 39 nets.

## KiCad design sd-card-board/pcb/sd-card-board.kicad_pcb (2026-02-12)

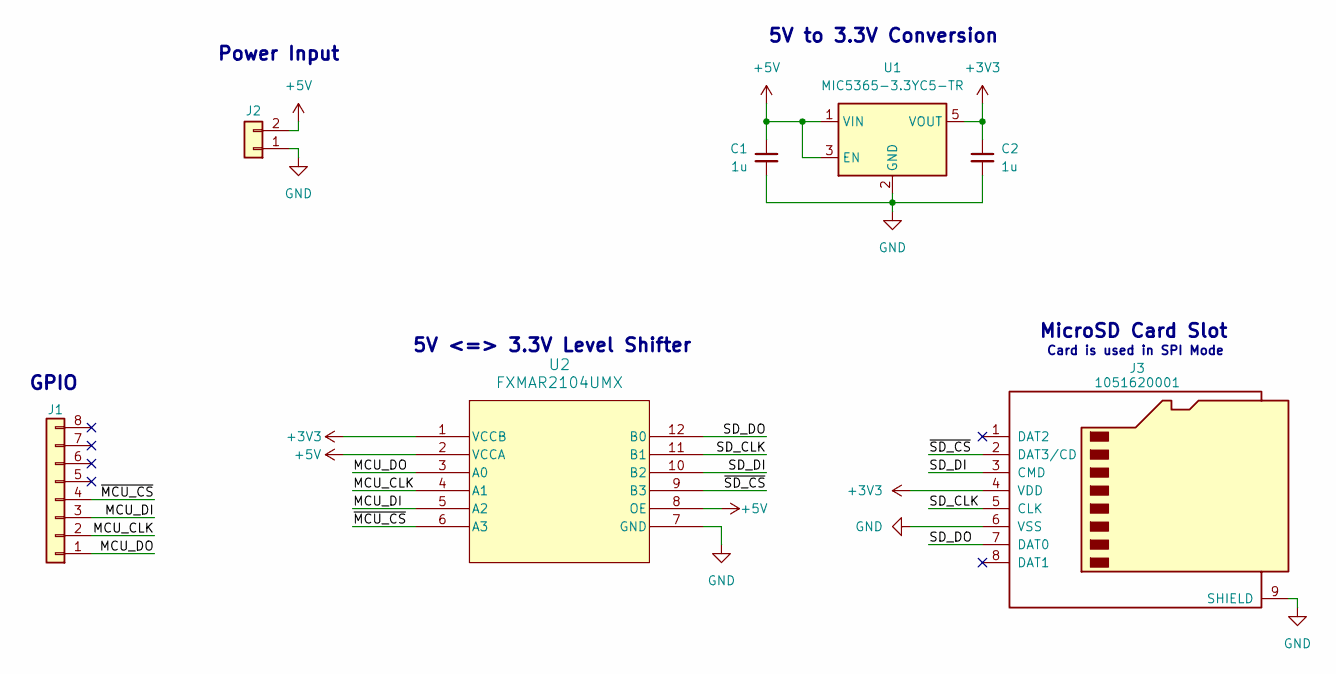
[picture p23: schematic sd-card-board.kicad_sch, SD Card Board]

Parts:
C1, C2: 1u; C_0402_1005Metric
J1: Conn_01x08; PinSocket_1x08_P1.27mm_Vertical
J2: Conn_01x02; PinSocket_1x02_P1.27mm_Vertical
J3: 1051620001; 105162-0001_MOL
U1: MIC5365-3.3YC5-TR; SOT-353_SC-70-5
U2: FXMAR2104UMX; ULTRATHIN_MLP_12L_ONS

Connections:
+3V3: C2.1, J3.4 (VDD), U1.5 (VOUT), U2.1 (VCCB)
+5V: C1.1, J2.2, U1.1 (VIN), U1.3 (EN), U2.2 (VCCA), U2.8 (OE)
/MCU_CLK: J1.2, U2.4 (A1)
/MCU_DI: J1.3, U2.5 (A2)
/MCU_DO: J1.1, U2.3 (A0)
/SD_CLK: J3.5 (CLK), U2.11 (B1)
/SD_DI: J3.3 (CMD), U2.10 (B2)
/SD_DO: J3.7 (DAT0), U2.12 (B0)
/~MCU_CS: J1.4, U2.6 (A3)
/~SD_CS: J3.2 (DAT3/CD), U2.9 (B3)
GND: C1.2, C2.2, J2.1, J3.6 (VSS), J3.9 (SHIELD), U1.2 (GND), U2.7 (GND)

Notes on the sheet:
MicroSD Card Slot
Power Input
5V <=> 3.3V Level Shifter
Card is used in SPI Mode
5V to 3.3V Conversion
GPIO

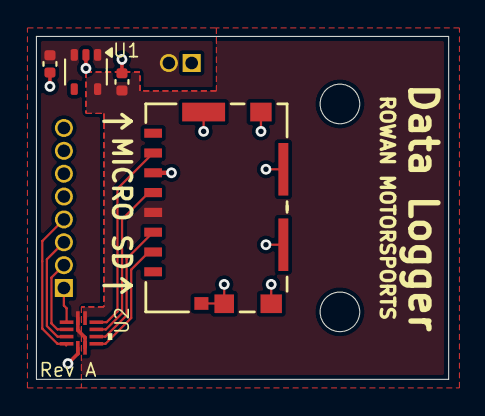
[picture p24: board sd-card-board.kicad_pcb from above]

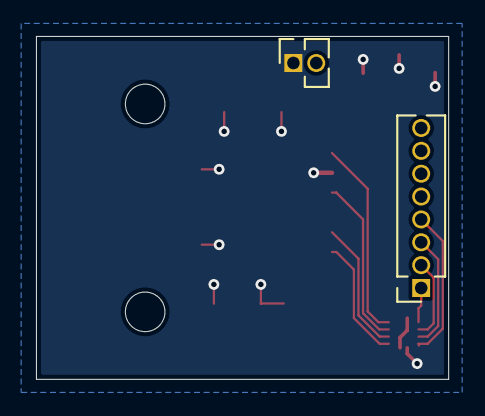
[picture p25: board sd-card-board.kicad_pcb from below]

Board: 2 copper layers, 22.9 x 19.1 mm, 7 parts (2 on the bottom side), 11 nets.

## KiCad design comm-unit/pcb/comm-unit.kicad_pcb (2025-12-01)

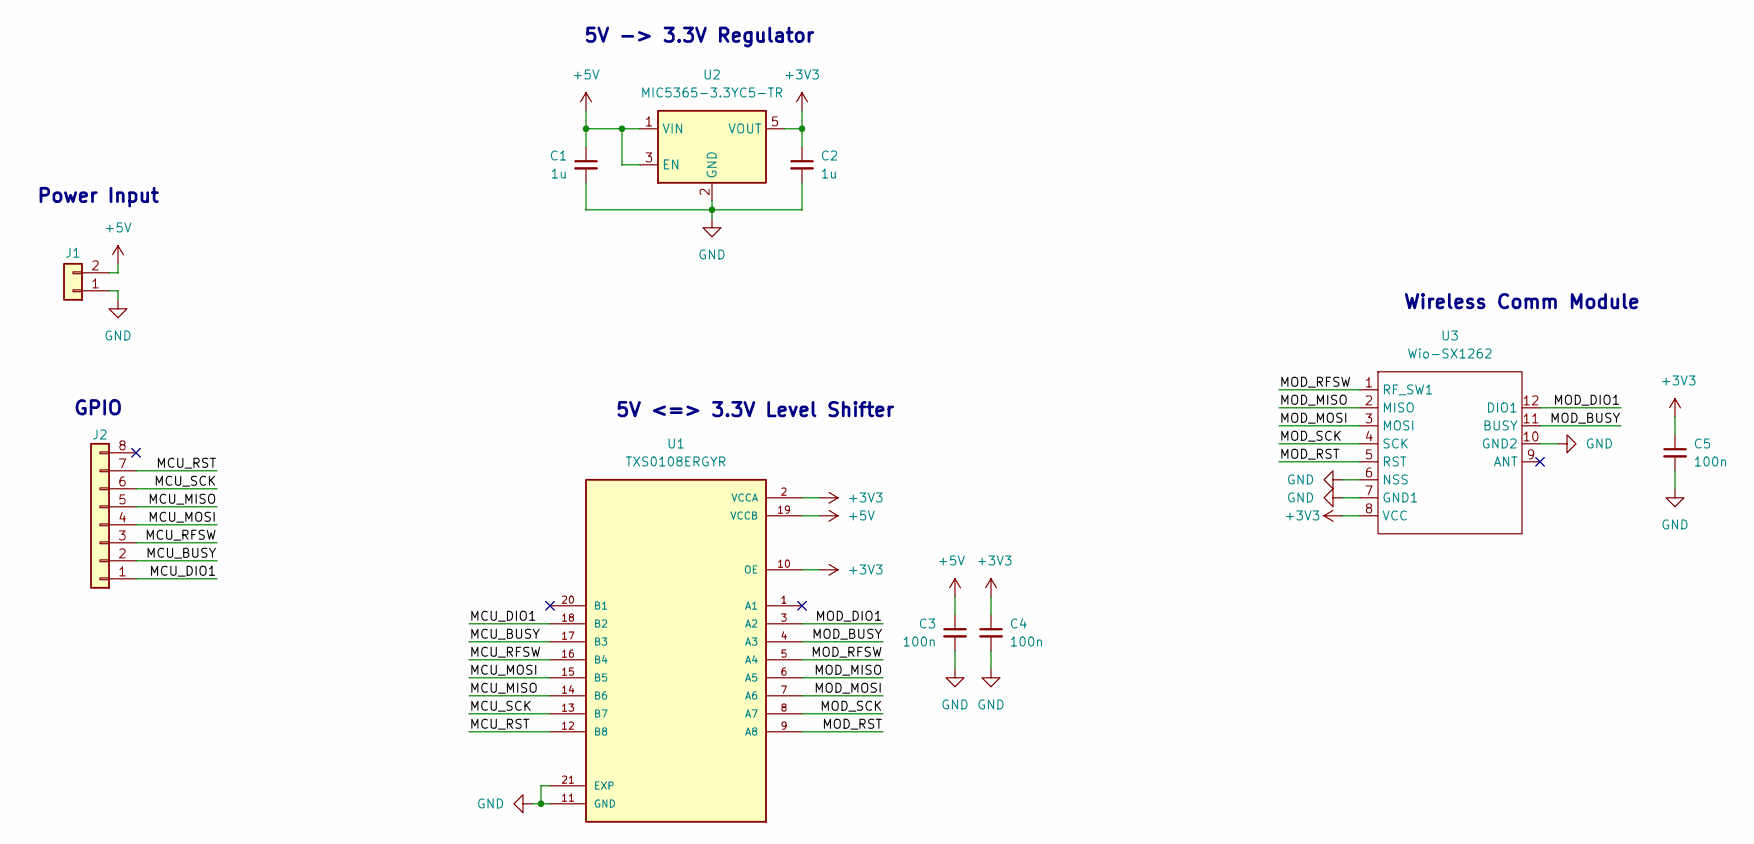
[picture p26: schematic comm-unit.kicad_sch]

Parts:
C1, C2: 1u; C_0402_1005Metric
C3, C4, C5: 100n; C_0402_1005Metric
J1: Conn_01x02; PinSocket_1x02_P1.27mm_Vertical
J2: Conn_01x08; PinSocket_1x08_P1.27mm_Vertical
U1: TXS0108ERGYR; IC_TXS0108ERGYR; PARTREV H
U2: MIC5365-3.3YC5-TR; SOT-353_SC-70-5
U3: Wio-SX1262; Wio-SX1262 PCB Package

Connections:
+3V3: C2.1, C4.1, C5.1, U1.2 (VCCA), U1.10 (OE), U2.5 (VOUT), U3.8 (VCC)
+5V: C1.1, C3.1, J1.2, U1.19 (VCCB), U2.1 (VIN), U2.3 (EN)
/MCU_BUSY: J2.2, U1.17 (B3)
/MCU_DIO1: J2.1, U1.18 (B2)
/MCU_MISO: J2.5, U1.14 (B6)
/MCU_MOSI: J2.4, U1.15 (B5)
/MCU_RFSW: J2.3, U1.16 (B4)
/MCU_RST: J2.7, U1.12 (B8)
/MCU_SCK: J2.6, U1.13 (B7)
/MOD_BUSY: U1.4 (A3), U3.11 (BUSY)
/MOD_DIO1: U1.3 (A2), U3.12 (DIO1)
/MOD_MISO: U1.6 (A5), U3.2 (MISO)
/MOD_MOSI: U1.7 (A6), U3.3 (MOSI)
/MOD_RFSW: U1.5 (A4), U3.1 (RF_SW1)
/MOD_RST: U1.9 (A8), U3.5 (RST)
/MOD_SCK: U1.8 (A7), U3.4 (SCK)
GND: C1.2, C2.2, C3.2, C4.2, C5.2, J1.1, U1.11 (GND), U1.21 (EXP), U2.2 (GND), U3.6 (NSS), U3.7 (GND1), U3.10 (GND2)

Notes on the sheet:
5V -> 3.3V Regulator
Wireless Comm Module
5V <=> 3.3V Level Shifter
Power Input
GPIO

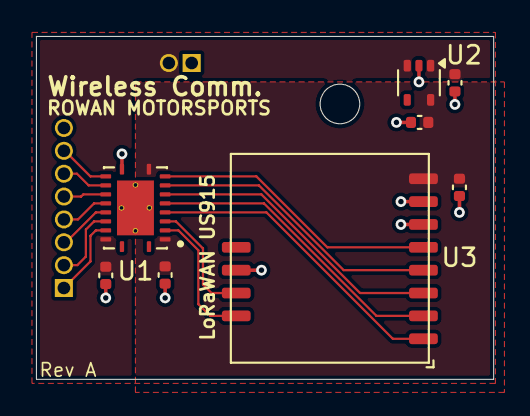
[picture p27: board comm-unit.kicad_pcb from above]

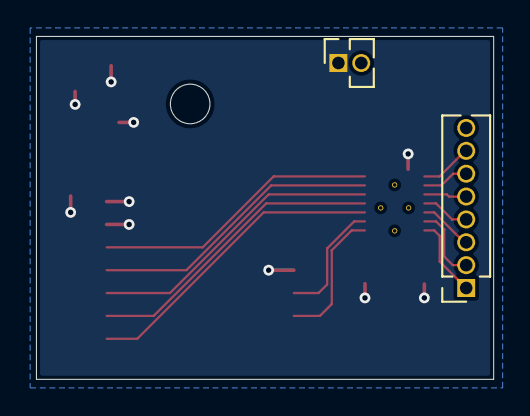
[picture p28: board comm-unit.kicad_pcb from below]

Board: 2 copper layers, 25.4 x 19.1 mm, 10 parts (2 on the bottom side), 17 nets.

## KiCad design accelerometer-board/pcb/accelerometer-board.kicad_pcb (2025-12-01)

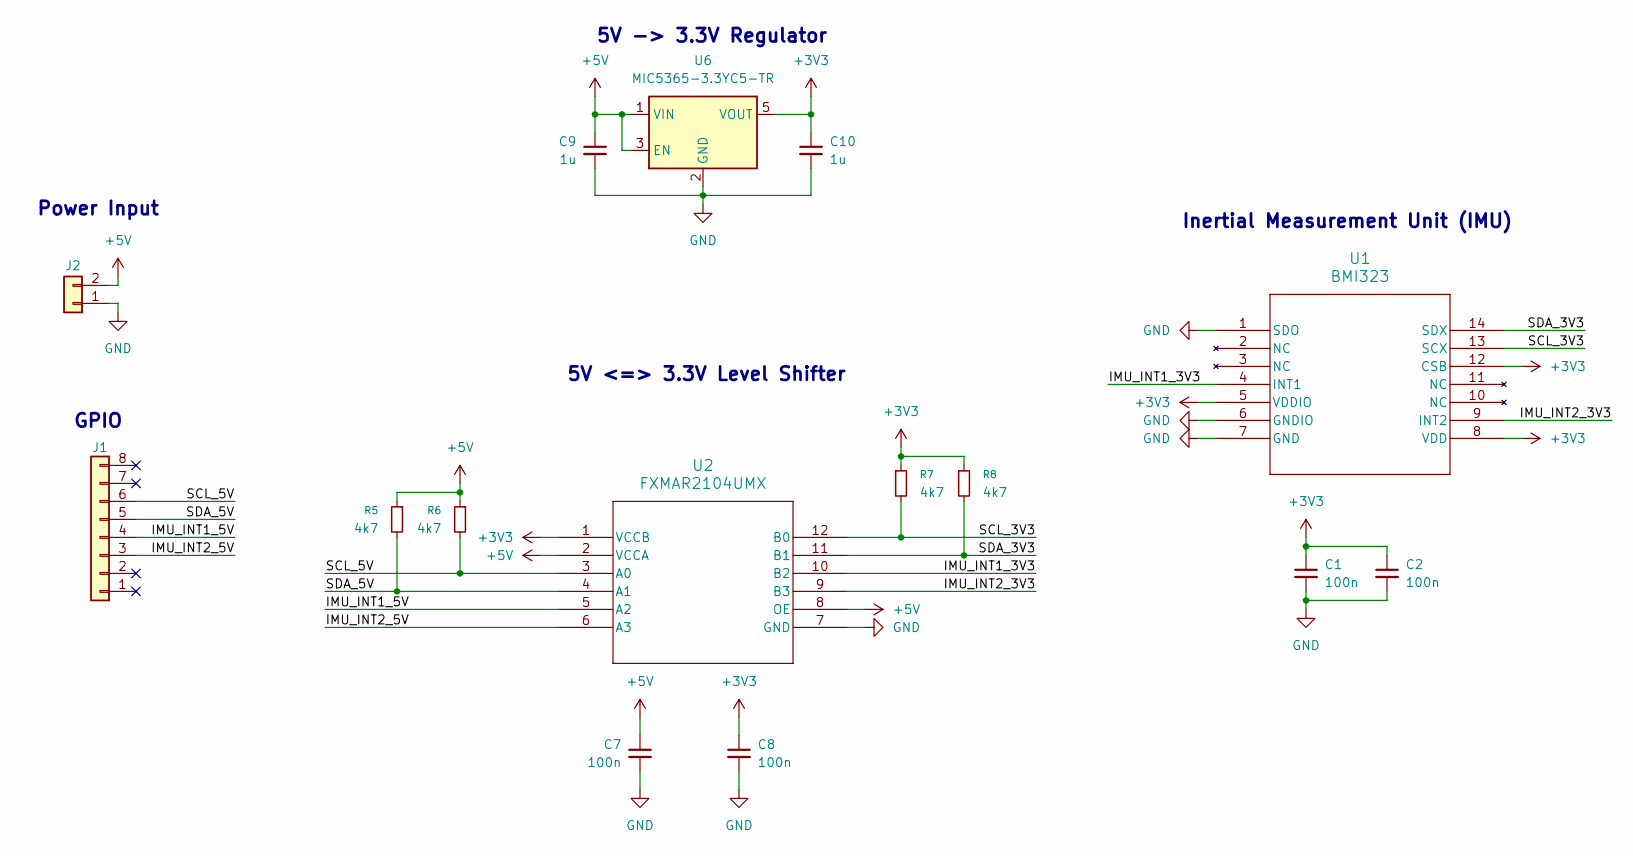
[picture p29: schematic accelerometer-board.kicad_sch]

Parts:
C1, C2, C7, C8: 100n; C_0402_1005Metric
C9, C10: 1u; C_0402_1005Metric
J1: Conn_01x08; PinSocket_1x08_P1.27mm_Vertical
J2: Conn_01x02; PinSocket_1x02_P1.27mm_Vertical
R5, R6, R7, R8: 4k7; R_0402_1005Metric
U1: BMI323; BMI323_BOS
U2: FXMAR2104UMX; ULTRATHIN_MLP_12L_ONS
U6: MIC5365-3.3YC5-TR; SOT-353_SC-70-5

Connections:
+3V3: C1.1, C2.1, C8.1, C10.1, R7.1, R8.1, U1.5 (VDDIO), U1.8 (VDD), U1.12 (CSB), U2.1 (VCCB), U6.5 (VOUT)
+5V: C7.1, C9.1, J2.2, R5.1, R6.1, U2.2 (VCCA), U2.8 (OE), U6.1 (VIN), U6.3 (EN)
/IMU_INT1_3V3: U1.4 (INT1), U2.10 (B2)
/IMU_INT1_5V: J1.4, U2.5 (A2)
/IMU_INT2_3V3: U1.9 (INT2), U2.9 (B3)
/IMU_INT2_5V: J1.3, U2.6 (A3)
/SCL_3V3: R7.2, U1.13 (SCX), U2.12 (B0)
/SCL_5V: J1.6, R6.2, U2.3 (A0)
/SDA_3V3: R8.2, U1.14 (SDX), U2.11 (B1)
/SDA_5V: J1.5, R5.2, U2.4 (A1)
GND: C1.2, C2.2, C7.2, C8.2, C9.2, C10.2, J2.1, U1.1 (SDO), U1.6 (GNDIO), U1.7 (GND), U2.7 (GND), U6.2 (GND)

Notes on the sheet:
Inertial Measurement Unit (IMU)
5V <=> 3.3V Level Shifter
5V -> 3.3V Regulator
GPIO
Power Input

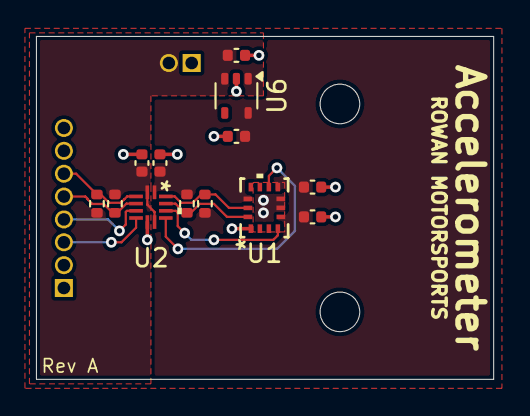
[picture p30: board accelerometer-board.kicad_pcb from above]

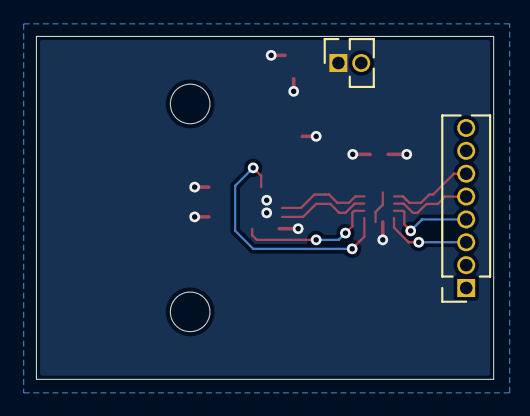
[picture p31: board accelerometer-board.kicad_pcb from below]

Board: 2 copper layers, 25.4 x 19.0 mm, 15 parts (2 on the bottom side), 11 nets.

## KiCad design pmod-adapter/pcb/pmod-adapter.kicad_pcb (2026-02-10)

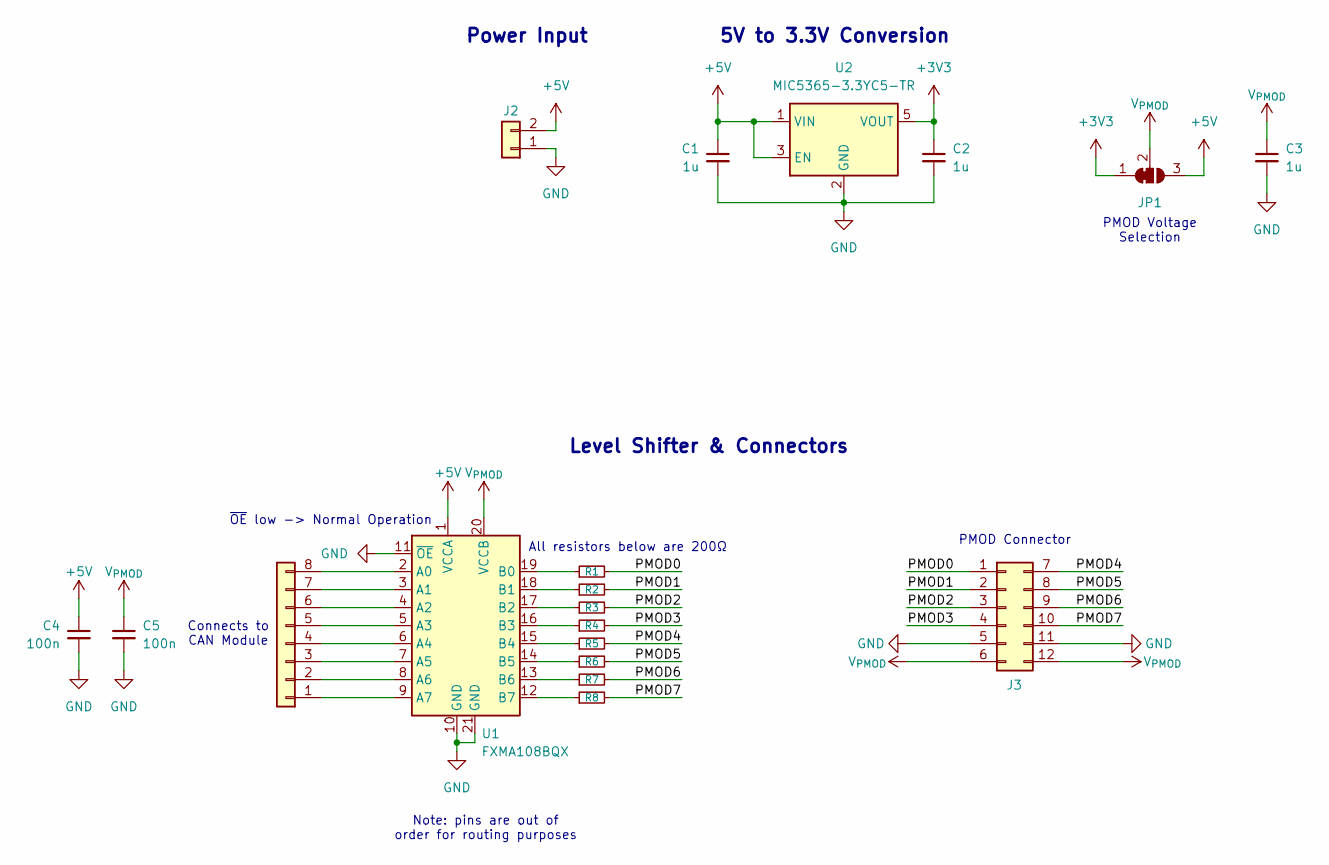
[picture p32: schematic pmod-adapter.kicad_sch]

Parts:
C1, C2, C3: 1u; C_0402_1005Metric
C4, C5: 100n; C_0402_1005Metric
J1: Conn_01x08; PinSocket_1x08_P1.27mm_Vertical
J2: Conn_01x02; PinSocket_1x02_P1.27mm_Vertical
J3: Conn_02x06_Top_Bottom; PinSocket_2x06_P2.54mm_Horizontal
JP1: SolderJumper_3_Bridged12; SolderJumper-3_P1.3mm_Bridged12_RoundedPad1.0x1.5mm
R1, R2, R3, R4, R5, R6, R7, R8: 200; R_0402_1005Metric
U1: FXMA108BQX; WQFN-20-1EP_2.5x4.5mm_P0.5mm_EP1x2.9mm
U2: MIC5365-3.3YC5-TR; SOT-353_SC-70-5

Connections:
+3V3: C2.1, JP1.1 (A), U2.5 (VOUT)
+5V: C1.1, C4.1, J2.2, JP1.3 (B), U1.1 (VCCA), U2.1 (VIN), U2.3 (EN)
/PMOD0: J3.1, R1.2
/PMOD1: J3.2, R2.2
/PMOD2: J3.3, R3.2
/PMOD3: J3.4, R4.2
/PMOD4: J3.7, R5.2
/PMOD5: J3.8, R6.2
/PMOD6: J3.9, R7.2
/PMOD7: J3.10, R8.2
GND: C1.2, C2.2, C3.2, C4.2, C5.2, J2.1, J3.5, J3.11, U1.10 (GND), U1.11 (~OE), U1.21 (GND), U2.2 (GND)
unnamed: J1.1, U1.9 (A7)
unnamed: J1.2, U1.8 (A6)
unnamed: J1.3, U1.7 (A5)
unnamed: J1.4, U1.6 (A4)
unnamed: J1.5, U1.5 (A3)
unnamed: J1.6, U1.4 (A2)
unnamed: J1.7, U1.3 (A1)
unnamed: J1.8, U1.2 (A0)
unnamed: R1.1, U1.19 (B0)
unnamed: R2.1, U1.18 (B1)
unnamed: R3.1, U1.17 (B2)
unnamed: R4.1, U1.16 (B3)
unnamed: R5.1, U1.15 (B4)
unnamed: R6.1, U1.14 (B5)
unnamed: R7.1, U1.13 (B6)
unnamed: R8.1, U1.12 (B7)
V_{PMOD}: C3.1, C5.1, J3.6, J3.12, JP1.2 (C), U1.20 (VCCB)

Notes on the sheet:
Power Input
Note: pins are out of order for routing purposes
All resistors below are 200Ω
Connects to CAN Module
PMOD Voltage Selection
Level Shifter & Connectors
~{OE} low -> Normal Operation
5V to 3.3V Conversion
PMOD Connector



Board: 2 copper layers, 23.7 x 19.1 mm, 19 parts (3 on the bottom side), 28 nets.

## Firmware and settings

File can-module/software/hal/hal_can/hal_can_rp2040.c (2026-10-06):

#include "hal_can.h"
#include <string.h>
#include <pico/stdlib.h>
#include <hardware/clocks.h>
#include <hardware/irq.h>
#include <can2040.h>

#define CAN_RX_PIN 2
#define CAN_TX_PIN 3
#define CAN_BITRATE 1000000
#define CAN_QUEUE_SIZE 32

static struct
{
    uint32_t pull_pos;
    volatile uint32_t push_pos;
    hal_can_frame_t queue[CAN_QUEUE_SIZE];
} can_rx_queue;

static struct can2040 cbus;

static void can_rx_callback(struct can2040* cd, uint32_t notify, struct can2040_msg* msg)
{
    (void)cd;

    if (notify == CAN2040_NOTIFY_RX)
    {
        uint32_t push_pos = can_rx_queue.push_pos;
        uint32_t pull_pos = can_rx_queue.pull_pos;

        if (push_pos + 1 == pull_pos || (push_pos + 1 - pull_pos == CAN_QUEUE_SIZE))
        {
            return;
        }

        hal_can_frame_t* frame = &can_rx_queue.queue[push_pos % CAN_QUEUE_SIZE];

        frame->is_extended = ((msg->id & CAN2040_ID_EFF) != 0);

        if (frame->is_extended)
        {
            frame->id = msg->id & 0x1FFFFFFF;
        }
        else
        {
            frame->id = msg->id & 0x7FF;
        }

        frame->size = (msg->dlc > 8) ? 8 : msg->dlc;
        memcpy(frame->data, msg->data, frame->size);

        can_rx_queue.push_pos = push_pos + 1;
    }
}

static void pio_irq_handler(void)
{
    can2040_pio_irq_handler(&cbus);
}

void hal_can_init(void)
{
    can_rx_queue.pull_pos = 0;
    can_rx_queue.push_pos = 0;

    can2040_setup(&cbus, 0);
    can2040_callback_config(&cbus, can_rx_callback);

    irq_set_exclusive_handler(PIO0_IRQ_0, pio_irq_handler);
    irq_set_priority(PIO0_IRQ_0, 1);
    irq_set_enabled(PIO0_IRQ_0, true);

    can2040_start(&cbus, clock_get_hz(clk_sys), CAN_BITRATE, CAN_RX_PIN, CAN_TX_PIN);
}

bool hal_can_send(uint32_t id, const uint8_t* data, size_t size)
{
    struct can2040_msg msg;
    memset(&msg, 0, sizeof(msg));

    if (id > 0x7FF)
    {
        msg.id = (id & 0x1FFFFFFF) | CAN2040_ID_EFF;
    }
    else
    {
        msg.id = id & 0x7FF;
    }

    msg.dlc = (size > 8) ? 8 : size;
    memcpy(msg.data, data, msg.dlc);

    return (can2040_transmit(&cbus, &msg) == 0);
}

size_t hal_can_available(void)
{
    uint32_t push = can_rx_queue.push_pos;
    uint32_t pull = can_rx_queue.pull_pos;

    return (size_t)(push - pull);
}

bool hal_can_receive(hal_can_frame_t* frame)
{
    if (frame == NULL)
    {
        return false;
    }

    uint32_t push = can_rx_queue.push_pos;
    uint32_t pull = can_rx_queue.pull_pos;

    if (push == pull)
    {
        return false;
    }

    *frame = can_rx_queue.queue[pull % CAN_QUEUE_SIZE];
    can_rx_queue.pull_pos = pull + 1;

    return true;
}

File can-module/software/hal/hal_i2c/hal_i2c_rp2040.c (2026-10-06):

#include "hal_i2c.h"
#include <pico/stdlib.h>
#include <hardware/i2c.h>

#define I2C_PORT i2c0
#define I2C_BAUD (100 * 1000)
#define I2C_SDA_PIN 4
#define I2C_SCL_PIN 5

void hal_i2c_init(void)
{
    i2c_init(I2C_PORT, I2C_BAUD);
    gpio_set_function(I2C_SDA_PIN, GPIO_FUNC_I2C);
    gpio_set_function(I2C_SCL_PIN, GPIO_FUNC_I2C);
    gpio_pull_up(I2C_SDA_PIN);
    gpio_pull_up(I2C_SCL_PIN);
}

bool hal_i2c_write(uint16_t address, const uint8_t* data, size_t size)
{
    int result = i2c_write_blocking(I2C_PORT, (uint8_t)address, data, size, false);

    return (result >= 0);
}

bool hal_i2c_read(uint16_t address, uint8_t* data, size_t size)
{
    if (data == NULL || size == 0)
    {
        return false;
    }

    int result = i2c_read_blocking(I2C_PORT, (uint8_t)address, data, size, false);

    return (result >= 0);
}

bool hal_i2c_write_read(uint16_t address, const uint8_t* wr_data, size_t wr_size, uint8_t* rd_data, size_t rd_size)
{
    if (rd_data == NULL || rd_size == 0)
    {
        return false;
    }

    int wr_result = i2c_write_blocking(I2C_PORT, (uint8_t)address, wr_data, wr_size, true);

    if (wr_result < 0)
    {
        return false;
    }

    int rd_result = i2c_read_blocking(I2C_PORT, (uint8_t)address, rd_data, rd_size, false);

    return (rd_result >= 0);
}

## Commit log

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2025-09-17 main_unit/hardware: Add in 25MHz crystal oscillator and capacitors
    [main_unit.kicad_sch]
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2025-09-18 main_unit/hardware: Fix STM32 to use LQFP-144 package instead of LQFP-100
    [main_unit.kicad_sch]
2025-09-18 main_unit/hardware: Add PCB to project with STM32 decoupling & bulk capacitors in rough positions
    [main_unit.kicad_pcb]
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2025-09-18 main_unit/hardware: Add in empty sheets for display, SDRAM, and debug
    [display.kicad_sch, main_unit.kicad_pcb, main_unit.kicad_sch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]
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2025-09-18 main_unit/hardware: Add in missing byte enable pins for SDRAM
    [main_unit.kicad_sch, sdram.kicad_sch]
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2025-09-18 main_unit/hardware: Set up rough position for SDRAM chip & capacitors
    [main_unit.kicad_pcb]
2025-09-18 main_unit/hardware: Add in display connector, expand LTDC to RGB888 (fixes pin error)
    [display.kicad_sch, main_unit.kicad_pcb, main_unit.kicad_sch]
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2025-09-19 main_unit/hardware: Add in backlight boost converter & LED driver skeleton from MAX chip datasheet
    [display.kicad_sch]
2025-09-19 main_unit/hardware: Fill out LED driver component values except for compensation circuit
    [display.kicad_sch]
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2025-09-20 main_unit/hardware: Get general layout of backlight driver components on PCB
    [main_unit.kicad_pcb]
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2025-09-22 main_unit/hardware: Connect LCD controller FAULT and PWM pin to STM32
    [main_unit.kicad_pcb, main_unit.kicad_sch]
2025-09-22 main_unit/hardware: Add in extra capacitor for BOSTMON, move things around slightly for MAX chip according to datasheet recommendations
    [display.kicad_sch, main_unit.kicad_pcb]
2025-09-23 main_unit/hardware: Rearrange components in boost converter to minimize loop area
    [main_unit.kicad_pcb]
2025-09-23 main_unit/hardware: Add in input power filtering and ST-Link connector
    [main_unit.kicad_pcb, main_unit.kicad_sch, power.kicad_sch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]
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2025-09-25 main_unit/hardware: Set up board as 4-layer, add ground and power planes
    [main_unit.kicad_pcb]
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2025-09-25 main_unit/hardware: More routing, specifically for CAN and decoupling caps
    [main_unit.kicad_pcb]
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2025-09-29 main_unit/hardware: Keep trying to find good way of routing out display
    [main_unit.kicad_pcb]
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2025-09-30 can-module: Add reset RC circuit
    [can-module.kicad_sch]
2025-09-30 can-module: Route power, gnd, and swd pins to test points
    [can-module.kicad_sch]
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2025-10-03 can-module: Add footprint to ATA6560, arrange so it is close to the MCU
    [can-module.kicad_pcb]
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2025-10-07 can-module: Move pins around, select GPIO pins, add test points for GPIOs
    [can-module.kicad_pcb, can-module.kicad_sch]
2025-10-07 can-module: Fix ATA6560 footprint to have 3D model
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2025-10-09 can-module: Rearrange components, update constraints for copper to board edge
    [can-module.kicad_pcb, can-module.kicad_sch]
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2025-10-09 can-module: Update ATA6560 schematic to have filled background
    [can-module.kicad_sch]
2025-10-09 can-module: Fix ground via pattern under ATA6560
    [can-module.kicad_pcb]
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2025-10-09 can-module: Move around traces to maximize power plane area
    [can-module.kicad_pcb]
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2025-10-13 can-module: Finalize pcb layout, fix errors and constraints
    [can-module.kicad_pcb]
2025-10-13 can-module: Update board layout to have 3x M2.5 screw holes
    [can-module.kicad_pcb]
2025-10-13 can-module: Add pull up/down resistors for all 8 GPIO pins
    [can-module.kicad_pcb, can-module.kicad_sch, gpio_resistors.kicad_sch]
2025-10-13 can-module: Comply with JLCPCB's via restrictions to avoid extra charges
    [can-module.kicad_pcb]
2025-10-13 can-module: Add back M2 mounting holes, finalize layout
    [can-module.kicad_pcb]
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2025-10-14 can-module: Convert GPIO header from 2x 4pin header to 1x 8pin
    [can-module.kicad_pcb, can-module.kicad_sch]
2025-10-14 can-module: Add actual Rowan Motorsports logo to PCB
    [can-module.kicad_pcb]
2025-10-15 can-module: Update PCB to match requirements for JLCPCB economic PCBA
    [can-module.kicad_pcb, can-module.kicad_sch, gpio_resistors.kicad_sch]
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2025-10-20 can-module: Separate KiCAD files into its own 'pcb' directory, create 'cad' directory with board step file
    [can-module.kicad_pcb, can-module.kicad_sch, can-module.step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]
2025-10-23 can-module: Make simple CAD model for bottom of enclosure
    [can-module.FCStd]
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2025-11-04 can-module: Adjust positioning for 5V daughterboard connector, add 3D models for daughterboard connector headers
    [can-module.kicad_pcb]
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2025-11-13 sd-card-board: Swap components, get general placement of components on PCB done
    [sd-card-board.kicad_pcb, sd-card-board.kicad_sch]
2025-11-13 sd-card-board: Route out PCB, add microSD card model
    [sd-card-board.kicad_pcb, sd-card-board.kicad_sch]
2025-11-13 sd-card-board: Fix connector spacing
    [sd-card-board.kicad_pcb]
2025-11-13 sd-card-board: Fully fix positioning issues
    [sd-card-board.kicad_pcb]
2025-11-18 accelerometer-board: Add to repo, design and route out board
    [accelerometer-board.kicad_pcb, accelerometer-board.kicad_sch]
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2025-11-25 accelerometer-board: Update to contain a single IMU chip
    [accelerometer-board.kicad_pcb, accelerometer-board.kicad_sch]
2025-11-29 can-module: Major changes to routing, placement; remove pull up/down resistors (use PIC32 internal resistors)
    [can-module.kicad_pcb, can-module.kicad_sch]
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2025-12-01 can-module: Change header size from 1mm spacing to 1.27mm spacing
    [can-module.kicad_pcb, can-module.kicad_sch]
2025-12-01 can-module: Resolve hole clearance issue
    [can-module.kicad_pcb]
2025-12-01 can-module: Re-attach gnd connection to main bulk cap for 5V
    [can-module.kicad_pcb]
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2025-12-01 can-module: Update CAN/PWR header to also be 0.127mm, move some things around to allow for wider min power plane width
    [can-module.kicad_pcb, can-module.kicad_sch]
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2026-02-12 comm-unit: Label correct pin numbers on README
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2026-02-12 sd-card-board: Switch pins around to ensure that all SPI pins are connected to the same peripheral
    [sd-card-board.kicad_sch]
2026-02-12 sd-card-board: Fix PCB, switch from using SERCOM0 to SERCOM2
    [sd-card-board.kicad_pcb, sd-card-board.kicad_sch]
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2026-02-14 can-module: Update CAN Module schematic to include power filtering & reverse polarity protection
    [can-module.kicad_sch]
2026-02-14 can-module: Update schematic and PCB to fully add in power filtering components
    [can-module.kicad_pcb, can-module.kicad_sch]
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2026-02-15 can-module: Add 1mm test point with tight spacing
2026-02-15 can-module: Use tight spacing test points on GPIO test points
    [can-module.kicad_sch]
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2026-02-15 can-module: Swap ideal diode package to be a KiCad standard package
    [can-module.kicad_pcb]
2026-02-16 can-module: Fix critical error bridging 5V to VDDCORE
    [can-module.kicad_pcb, can-module.kicad_sch]
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2026-02-16 can-module: Update CAN module to have selectable GPIO voltage (3.3V or 5V)
    [can-module.kicad_pcb, can-module.kicad_sch]
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2026-02-17 can-module: Flip indicator LED around so that anode is always 5V
    [can-module.kicad_pcb, can-module.kicad_sch]
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2026-02-18 can-module: Revert back to only having 5V logic on the board
    [can-module.kicad_pcb, can-module.kicad_sch]
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2026-04-13 can-module/pcb: Fix references to assets in README
2026-04-14 can-module/software: Fix GPIO_CAN_STANDBY pin number in README
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
